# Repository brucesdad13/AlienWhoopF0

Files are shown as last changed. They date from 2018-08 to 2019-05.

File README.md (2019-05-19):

# AlienWhoopF0

IMAGE AlienWhoop ZER0

# AlienWhoopF0 Features :alien:
AlienWhoop F0 (code name ZER0) flight controller for Tiny Whoop™, Blade Inductrix™, Eachine™, BetaFPV™, and other micro brushed quadcopter frames. Best in class flight controller running NotFastEnuf Silverware--surface mount soldering required.

* Value-line ST Microelectronics ARM® 32-bit Cortex®-M0 CPU, frequency up to 48 MHz (64MHz with overclocking)
* Invensense MPU-6881 Six-Axis (Gyro + Accelerometer) low power consumption MEMS MotionTracking™ Device
* Latest NotFastEnuf Silverware firmware running the ALIENZER0 target with optional Torque Boost
* Fairchild Semiconductor FDMA410NZ MOSFET with 9.5A continuous and 24A burst brushed motor insanity (8.5mm coreless scream)
* USART1 RX and TX solder pads for external receiver; solder pads for GPIO A13 and A14 for programmable LED strip (SUPER COOL) using WS2812B RGB or low voltage beeper
* Choice of external serial receivers. Officially supporting most SBUS, DSMX, DSM2 and Bayang SPI receivers.

## DIY Flight Controller :alien:
If you fancy doing it yourself (DIY), and have the right equipment and patience, building an AlienWhoop ZER0 from scratch can be tremendously satisfying--though not for the faint of heart. After doing your homework the first step is to place an order for blank PCBs from [OSH Park](https://oshpark.com/shared_projects/yiRaAjtL):
* We recommend ordering the 2oz copper 0.8mm thickness PCB
  * *It takes about three weeks to make the thin boards which allows plenty of time to order components from the bill of materials in the resources folder.*

## Official Facebook page :alien:
AlienWhoop has a Facebook page and it's our preferred way to engage with you and keep you updated. Please Like and/or Follow Us for regular updates in your status feed related to AlienWhoop, DIY electronics, and micro brushed quadcopter related posts.
* http://fb.me/alienwhoop/
* Instagram @alienwhoop

## See the AlienWhoop ZER0 in action on YouTube :alien:
IMAGE AlienWhoop ZER0 (https://www.youtube.com/watch?v=PHuMYIHKqiw)

## Acknowledgements :alien:

The AlienWhoop ZER0 Dev Team:

* Brucesdad13 (Charlie)
* Excalibur (Galen)
* MontiFPV (Michael)
* NotFastEnuf (Travis)
* VelcoFPV (Brian)

The sources of inspiration for this board are Lance's AlienFlight F3 Brushed
Quad (CC-BY-SA license) and the Silverware flight controller firmware (MIT
license).

Archival copy of Lance's AlienFlight F3 Eagle CAD Projects
* http://github.com/brucesdad13/AlienFlightArchive

NotFastEnuf's fork of Silverware flight controller firmware:
* https://github.com/NotFastEnuf/NFE_Silverware

~ Please note: **AlienWhoop** is not affiliated with nor endorsed by AlienFlight or forks of Lance's work such as AlienFlight NG. The use of Alien in the name and the alien head vector graphic used on the board silkscreen are nods to the lineage of this remix and to the work of Lance and others who created the conditions for this project to arise. Likewise, AlienWhoop is not affiliated with nor endorsed by Tiny Whoop. The Whoop in the name comes from Jesse Perkin's fantastic Tiny Whoop ("a small first-person-view aircraft that truly allows you to feel the gift of flight and the feeling of being tiny" [tinywhoop.com]) and is simply a nod to his efforts and the TW community worldwide.

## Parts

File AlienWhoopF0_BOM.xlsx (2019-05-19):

Qty | Value | Part Num | Package | Parts | Comments
6 | 0.1uF | GCM155R71C104KA55D | 0402 | C1, C4, C5, C9, C11, C24 | Can substitute
5 | 10K | RC0402FR-0710KL | 0402 | R1, R6, R7, R8, R9 | Can substitute
4 | 53047-02 | 53047-0210 | 53047-02 | M0, M1, M2, M3 | Molex motor plugs; can substitute 2-pin 1.25mm pitch shrouded
4 | FDMA410NZ | FDMA410NZ | MICROFET-2X2 | Q0, Q1, Q2, Q3 | For better performance use Infineon IRFHS8342TRP
3 | 22UF | JMK212BJ226MG-T | YUDEN-CAP-0805 | C25, C26, C27 | Can substitute
2 | 2K7 | AC0402JR-072K7L | 0402 | R2, R3 | For I2C gyro; can substitute/change value to find optimal performance
2 | 10nF | GCM155R71H103KA55D | 0402 | C3, C10 | Can substitute
2 | 1uF | GRM155C71A105KE11D | 0402 | C2, C22 | Can substitute
2 | 10UF | JMK212AB7106KG-T | YUDEN-CAP-0805 | C7, C8 | Can substitute
1 | 3.3V | AP2210N-3.3TRG1 | SOT-23 | Q5 | Don't use AP2210N! Use LM6206N3 (662K); can be harvested from toy fc/tx
1 | BLUE | APHCM2012QBC/D-F01 | SMD-CHIP-LED-0805 | LED0 | Blue LED; can substitute--update CLR as necessary
1 | 1K | AT0402BRD071KL | 0402 | R5 | For voltage divider; can substitute
1 | 2K | AT0402BRE072KL | 0402 | R10 | For voltage divider; can substitute
1 | 1UH | DFE201612E-1R0M=P2 | DFE201612E-INDUCTOR | L1 | Can substitute
1 | 2.2uF | GRM155C70J225KE11D | 0402 | C23 | Can substitute
1 | 4.7uF | GRM155R60G475ME47J | 0402 | C6 | Can substitute
1 | MPU-6881 | MPU-6881 | QFN24_PAD | U1 | Can substitute Invensense MPU-6500, MPU-9250, etc; update NFE gyro code
1 | 200R | RC0402JR-7D200RL | 0402 | R4 | Current limiting resistor (CLR) for LED0; match to LED0 datasheet
1 | STM32F030F4P | STM32F030F4P6TR | TSSOP20-I | U2 | MCU
1 | TPS63061DSC5V | TPS63061DSCR | TPS6306X | U7 | Buck boost

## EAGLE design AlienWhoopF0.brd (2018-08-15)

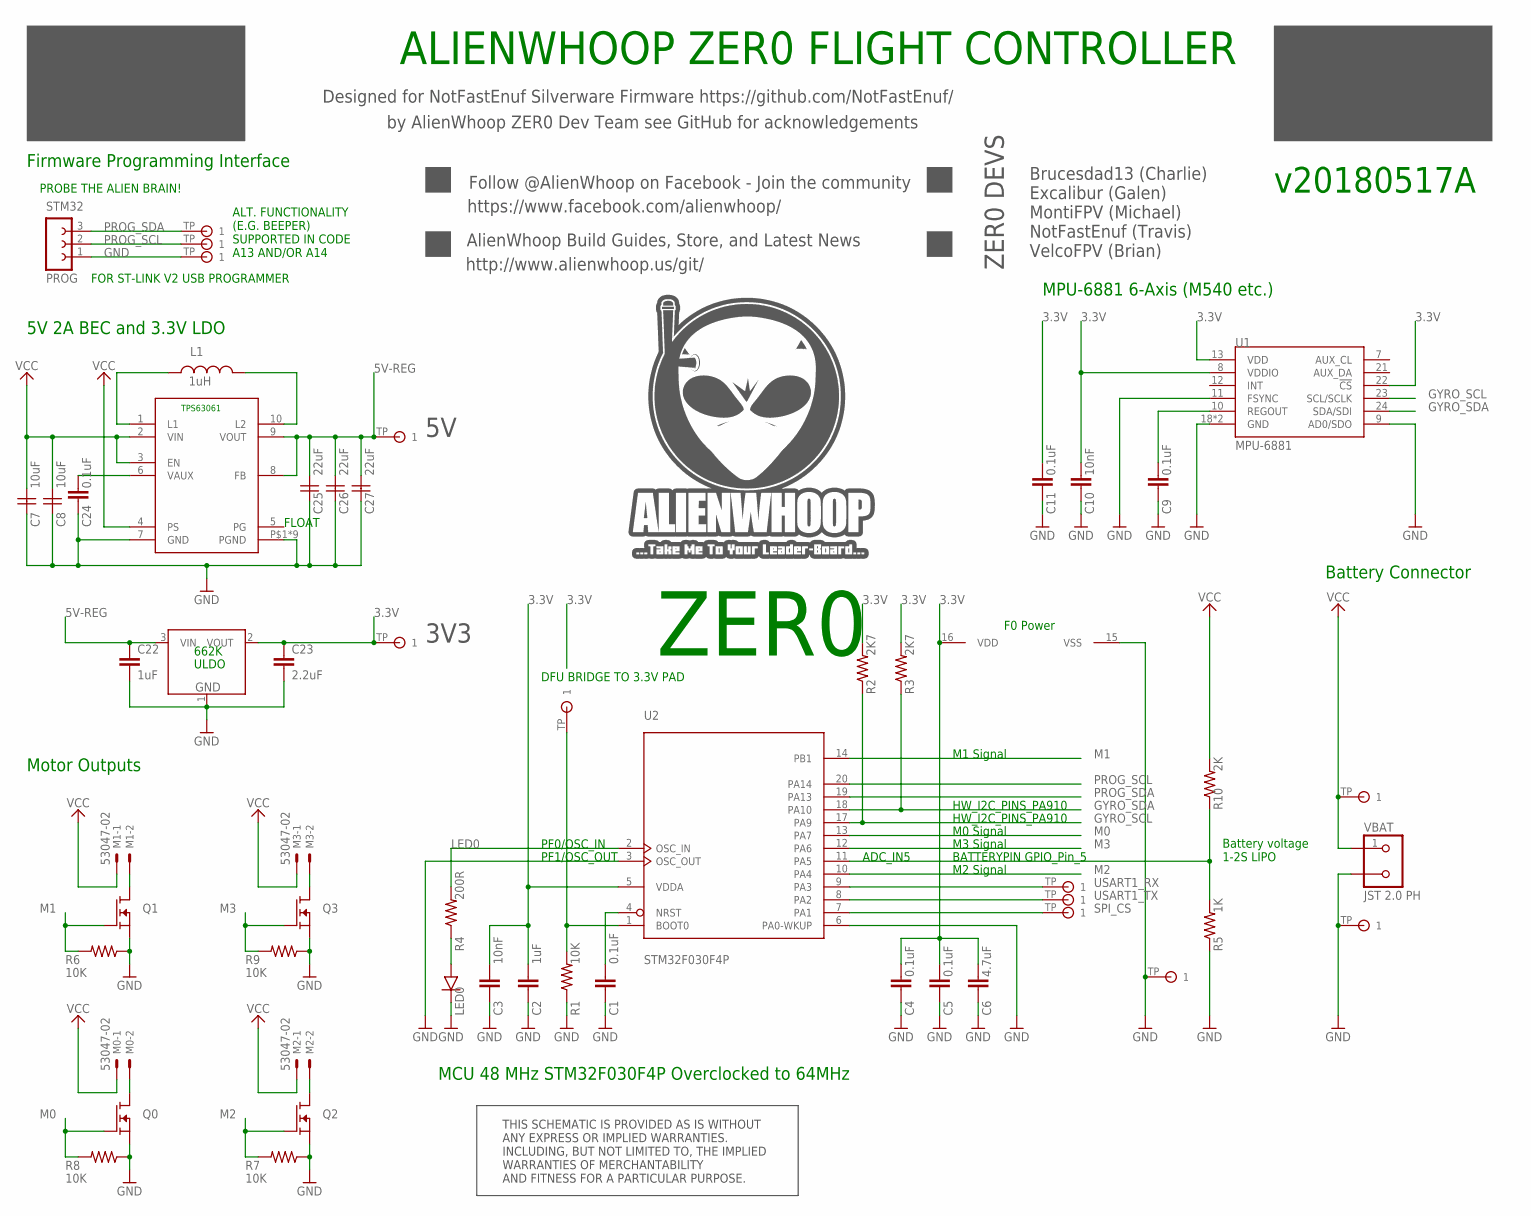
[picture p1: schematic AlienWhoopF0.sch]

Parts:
3.3V2, 5V2: TESTPAD
+: TESTPAD
-: TESTPAD
A13, A14: TESTPAD
C1, C4, C5, C9, C11, C24: 0.1uF; 0402; PARTNO GCM155R71C104KA55D
C2, C22: 1uF; 0402; PARTNO GRM155C71A105KE11D
C3, C10: 10nF; 0402; PARTNO GCM155R71H103KA55D
C6: 4.7uF; 0402; PARTNO GRM155R60G475ME47J
C7, C8: 10uF; YUDEN-CAP-0805
C23: 2.2uF; 0402; PARTNO GRM155C70J225KE11D
C25, C26, C27: 22uF; YUDEN-CAP-0805
DFU: TESTPAD
GND23: TESTPAD
GND@2: TESTPAD
L1: 1uH; DFE201612E-INDUCTOR
LED0: BLUE; SMD-CHIP-LED-0805
M0, M1, M2, M3: 53047-02
Q0, Q1, Q2, Q3: FDMA410NZ; MICROFET-2X2
Q5: 3.3V; SOT-23; PARTNO AP2210N-3.3TRG1
R1, R6, R7, R8, R9: 10K; 0402; PARTNO RC0402FR-0710KL
R2, R3: 2K7; 0402; PARTNO AC0402JR-072K7L
R4: 200R; 0402; PARTNO RC0402JR-7D200RL
R5: 1K; 0402; PARTNO AT0402BRD071KL
R10: 2K; 0402; PARTNO AT0402BRE072KL
SPI_CS: TESTPAD
STM32: PROG; FE03-1
U1: MPU-6881; QFN24_PAD; PARTNO MPU-6881
U2: STM32F030F4P; TSSOP20-I; PARTNO STM32F030F4P6TR
U7: TPS63061DSC5V; TPS6306X; PARTNO TPS63061DSCR
U$13, U$14: TESTPAD
VBAT: JST 2.0 PH; S2B-PH-K-S

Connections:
3.3V: 3.3V2.TP, C2.1, C3.1, C4.1, C5.1, C6.1, C10.1, C11.2, C23.1, Q5.2 (VOUT), R2.2, R3.2, U1.8 (VDDIO), U1.13 (VDD), U1.22 (!CS), U2.5 (VDDA), U2.16 (VDD)
5V-REG: 5V2.TP, C22.1, C25.1, C26.1, C27.1, Q5.3 (VIN), U7.8 (FB), U7.9 (VOUT)
BOOT: DFU.TP, R1.2, U2.1 (BOOT0)
GND: -.TP, C1.2, C2.2, C3.2, C4.2, C5.2, C6.2, C7.2, C8.2, C9.2, C10.2, C11.1, C22.2, C23.2, C24.2, C25.2, C26.2, C27.2, GND23.TP, GND@2.TP, LED0.C, Q0.S, Q0.S1 (S), Q1.S, Q1.S1 (S), Q2.S, Q2.S1 (S), Q3.S, Q3.S1 (S), Q5.1 (GND), R1.1, R5.1, R6.1, R7.1, R8.1, R9.1, STM32.1, U1.9 (AD0/SDO), U1.11 (FSYNC), U1.18 (GND), U1.20 (GND), U2.3 (OSC_OUT), U2.6 (PA0-WKUP), U2.15 (VSS), U7.7 (GND), U7.P$1 (PGND), U7.P$2 (PGND), U7.P$3 (PGND), U7.P$4 (PGND), U7.P$5 (PGND), U7.P$17 (PGND), U7.P$18 (PGND), U7.P$21 (PGND), U7.P$22 (PGND), VBAT.2
GYRO_SCL: R2.1, U1.23 (SCL/SCLK), U2.17 (PA9)
GYRO_SDA: R3.1, U1.24 (SDA/SDI), U2.18 (PA10)
L1A: L1.P$1 (1), U7.1 (L1)
L1B: L1.P$2 (2), U7.10 (L2)
LED: LED0.A, R4.1
LED0: R4.2, U2.2 (OSC_IN)
M0: Q0.G, R8.2, U2.13 (PA7)
M0G: M0.2, M0.2S, Q0.D, Q0.D1 (D), Q0.D2 (D), Q0.D3 (D), Q0.D4 (D)
M1: Q1.G, R6.2, U2.14 (PB1)
M1G: M1.2, M1.2S, Q1.D, Q1.D1 (D), Q1.D2 (D), Q1.D3 (D), Q1.D4 (D)
M2: Q2.G, R7.2, U2.10 (PA4)
M2G: M2.2, M2.2S, Q2.D, Q2.D1 (D), Q2.D2 (D), Q2.D3 (D), Q2.D4 (D)
M3: Q3.G, R9.2, U2.12 (PA6)
M3G: M3.2, M3.2S, Q3.D, Q3.D1 (D), Q3.D2 (D), Q3.D3 (D), Q3.D4 (D)
NRST: C1.1, U2.4 (NRST)
PROG_SCL: A14.TP, STM32.2, U2.20 (PA14)
PROG_SDA: A13.TP, STM32.3, U2.19 (PA13)
REGOUT: C9.1, U1.10 (REGOUT)
SPI_CS: SPI_CS.TP, U2.7 (PA1)
USART1_RX: U2.9 (PA3), U$13.TP
USART1_TX: U2.8 (PA2), U$14.TP
VAUX: C24.1, U7.6 (VAUX)
VCC: +.TP, C7.1, C8.1, M0.1, M0.1S, M1.1, M1.1S, M2.1, M2.1S, M3.1, M3.1S, R10.2, U7.2 (VIN), U7.3 (EN), U7.4 (PS), VBAT.1
VOLTDIV: R5.2, R10.1, U2.11 (PA5)

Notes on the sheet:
ADC_IN5
HW_I2C_PINS_PA910
BATTERYPIN GPIO_Pin_5
DFU BRIDGE TO 3.3V PAD
Battery voltage 1-2S LIPO
F0 Power
PF0/OSC_IN
PF1/OSC_OUT
PROBE THE ALIEN BRAIN!
FOR ST-LINK V2 USB PROGRAMMER
Designed for NotFastEnuf Silverware Firmware https://github.com/NotFastEnuf/
https://www.facebook.com/alienwhoop/
Follow @AlienWhoop on Facebook - Join the community
by AlienWhoop ZER0 Dev Team see GitHub for acknowledgements
http://www.alienwhoop.us/git/
AlienWhoop Build Guides, Store, and Latest News
ALIENWHOOP ZER0 FLIGHT CONTROLLER
v20180517A
THIS SCHEMATIC IS PROVIDED AS IS WITHOUT ANY EXPRESS OR IMPLIED WARRANTIES. INCLUDING, BUT NOT LIMITED TO, THE IMPLIED WARRANTIES OF MERCHANTABILITY AND FITNESS FOR A PARTICULAR PURPOSE.
Motor Outputs
MPU-6881 6-Axis (M540 etc.)
Battery Connector
5V 2A BEC and 3.3V LDO
Firmware Programming Interface
ZER0
MCU 48 MHz STM32F030F4P Overclocked to 64MHz
Brucesdad13 (Charlie) Excalibur (Galen) MontiFPV (Michael) NotFastEnuf (Travis) VelcoFPV (Brian)
ZER0 DEVS
3V3
ALT. FUNCTIONALITY (E.G. BEEPER) SUPPORTED IN CODE A13 AND/OR A14
M2 Signal
M0 Signal
M1 Signal
M3 Signal
FLOAT
662K

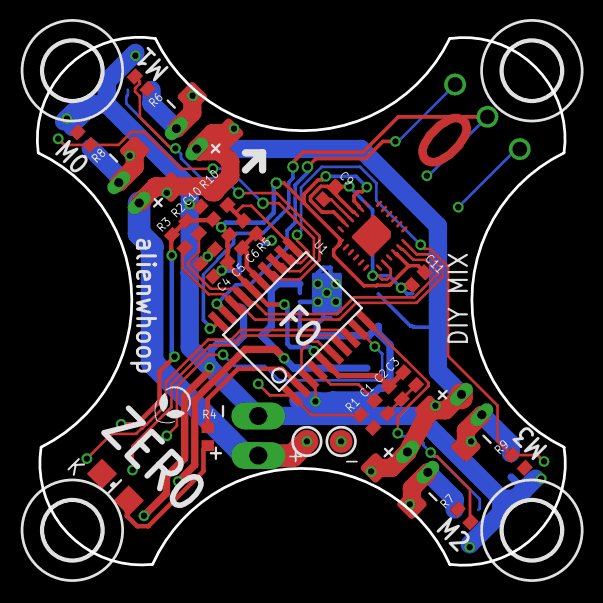
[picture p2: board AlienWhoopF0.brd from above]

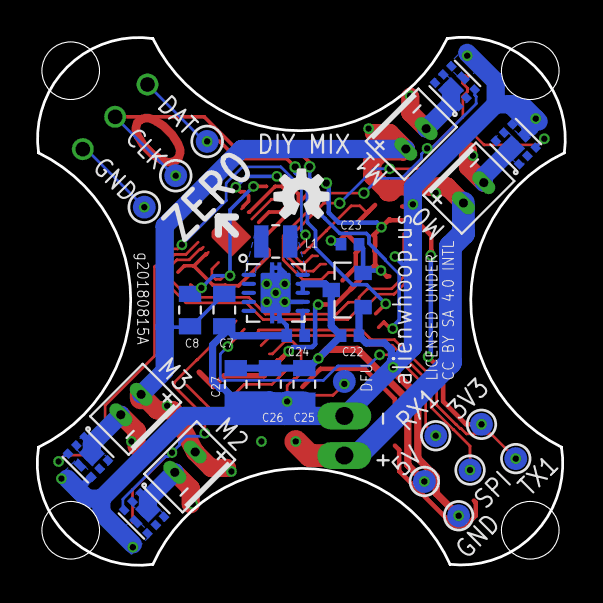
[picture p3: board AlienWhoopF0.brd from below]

Board: 2 copper layers, 29.3 x 29.3 mm, 60 parts (31 on the bottom side), 28 nets.

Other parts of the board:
LOGO3: OSHW-LOGOS; OSHW-LOGO-S
U$1, U$2, U$3, U$4: 3,2

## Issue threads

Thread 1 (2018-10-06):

BOM

mgrapiniak, 2018-10-06:
Hi :)

Resource folder is mentioned in README however there istn’t any.
Cheers!

brucesdad13, 2019-02-03:
Thanks! I'll update the README etc. I actually have some other changes to
push out like sharper corners ...

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

Closed 2019-05-19.

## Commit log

2018-08-15 Initial commit of the AlienWhoop ZER0 DIY MIX. #sendit #alienwhoopzer0
    [AlienWhoopF0.brd, AlienWhoopF0.sch]
2019-05-19 Sharpened up corners to better grip grommets during crashes--consistent with manuf. fc. Added BOM as requested; closes PR#2
    [AlienWhoopF0_BOM.xlsx]
2019-05-19 Update README.md
    Updated board preview image and OSH Park PCB shared project link

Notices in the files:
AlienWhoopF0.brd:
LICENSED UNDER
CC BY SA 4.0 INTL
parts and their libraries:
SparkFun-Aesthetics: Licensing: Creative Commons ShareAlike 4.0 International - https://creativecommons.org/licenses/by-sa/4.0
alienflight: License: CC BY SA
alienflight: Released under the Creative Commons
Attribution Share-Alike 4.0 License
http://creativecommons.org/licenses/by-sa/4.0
